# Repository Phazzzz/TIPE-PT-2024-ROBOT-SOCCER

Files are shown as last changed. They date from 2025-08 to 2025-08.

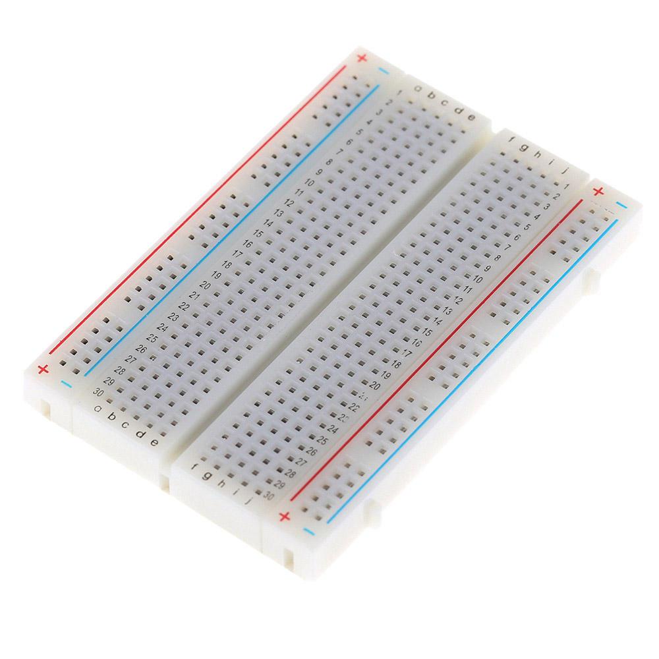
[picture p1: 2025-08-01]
Images illustrations/93206-desc-Quality-Solderless-Breadboard-400-Tie-Point-PCB-BreadBoard-for-Arduino-Interconnect-any-Components-with-20-29-AWG-(0.3-0.8)-wire-7-224400689.jpg

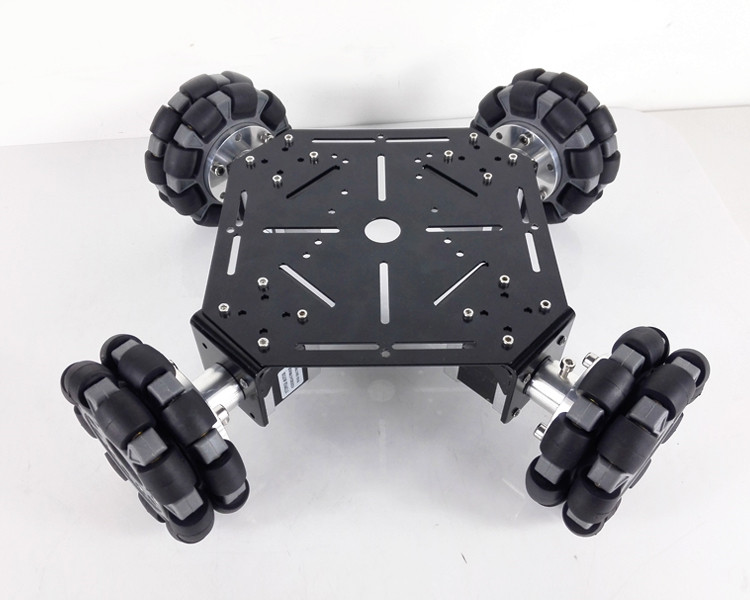
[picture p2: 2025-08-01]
Images illustrations/MT200S-4WD-100mm-Omni-Wheels-Robot-Car-Chassis-Stainsteel-Frame-Big-Power-Motor-For-DIY-Toy-2979076087.jpg

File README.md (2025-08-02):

# TIPE-PT-2024-ROBOT-SOCCER
Repo d'archive pour mon projet de TIPE que j'ai réalisé entre février 2023 et juin 2024 lorsque j'étais en prépa PT et pour lequel j'ai obtenu la note de 19,9/20. J'espère qu'il pourra aider de futurs taupins ! 

## L'histoire de ce TIPE

Comme tout taupin, je devais réaliser un projet de TIPE. C'était pour moi l'occasion de travailler sur un sujet qui plaisait réellement au milieu de tout les cours de prépas - qui ne sont pas tous passionnants, et dont l'utilité n'est pas toujours évidente. Ce projet a été mon exutoire en PTSI lorsque je n'avais pas envie de travailler mon prochain DS. 

Le thème de TIPE pour l'année 2023/2024 était "Jeux et sports", je savais dès le début que je voulais travailler sur un robot (même si je n'y connaissais strictement rien à l'époque) et ma première idée était de faire un robot de combat lol, mes profs me l'on déconseillé, car les sujets liés aux armes sont trop clivants auprès des correcteurs. La principale condition qu'ils m'avaient imposée était qu'il existe une ligue sportive pour le robot que j'allais réaliser. Je suis donc très rapidement tombé sur la Robocup, ce qui était la justification parfaite pour placer mon TIPE dans le thème de l'année. 

J'ai majoritairement travaillé sur ce projet durant l'année de PTSI (CF le DOT), j'ai d'abord commencé par faire le maximum de recherche sur comment fonctionne un robot pendant 1 mois et demi, puis j'ai acheté les composants pour faire un premier assemblage du robot, qui après à peu près 1 mois et de demie d'assemblage et de codage s'est avéré ne pas fonctionner. Durant l'année de PT, j'ai principalement fait de petites améliorations, changer quelques composants. J'ai surtout travaillé dessus entre les écrits et la date de rendu du projet (environ 3 semaines), j'ai passé 1 semaine à essayer de l'améliorer le plus possible, 1 semaine à faire toutes les expériences possibles pour justifier tout ce qui fonctionne et surtout tout ce qui ne fonctionne, puis 1 semaine pour faire le Powerpoint et travailler la présentation. 

D'après mon professeur de SI, la durée d'un bon TIPE est d'à peu près 50 à 70 h, personnellement, je suis plus proche des 350 h d'après mes estimations… Je n'ai évidemment aucun regret, mais je ne sais pas pour autant si je conseillerais d'en faire autant, car au final, mon projet était tellement ambitieux que la majorité du travail n'était pas présentable mais nécessaire à la réalisation du projet. Ce qui rajoute beaucoup de travail lors de la préparation de la présentation. D'ailleurs, je n'ai pas eu le temps de bien présenter la section "Présentation du robot" par manque de temps, je n'ai pu que la survoler, car je priorisais la conclusion.

## Pourquoi j'ai réussi cette épreuve selon moi 

#### J'ai kiffé réaliser ce projet
Comme dit plus haut, je me suis régalé pendant ce projet, j'ai tout réalisé moi-même, dessiner, imprimer des pièces en 3D, sélectionner les composant, faire l'assemblage, etc. Et j'ai bien appuyé sur ce point là pendant ma présentation. La pire chose qui puisse arriver pour un TIPE ambitieux est que le jury ne crois pas que vous l'ayez fais vous-même. La première question que le jury m'a posée était : "Où avez-vous acheté le robot ?", donc pendant toute la phase de réponse aux questions, j'ai donnée le maximum d'élément personnel pour justifier le fait que j'ai tout fais moi-même, sortir des photos, donner citer les références des composants (quand on a autant travaillé dessus ça finit par rentrer…), etc.

#### Faire un TIPE "original" et personnel
Un de mes profs en école me disait qu'il était correcteur l'année où j'ai passé mon TIPE, il a corrigé près de 70 TIPE portant sur la raquette de paddle… Donc, nécessairement, il devient difficile de ne pas s'endormir et tu deviens très exigeant dans la correction, la moyenne des notes qu'il donnait étaient autour de 9, et 14.5 étaient une bonne note selon lui.
Alors que lors de mon passage, avant de rentrer dans la salle, le correcteur m'avait très clairement fait savoir qu'il était curieux d'entendre mon travail. Alors qu'il y a beaucoup de TIPE qui sont plus technique, réalisé par des personnes plus talentueuses que moi, je pense que l'avantage de TIPE est que le sujet est plutôt cool. 

#### Être capable de tout justifier 
Ce que les correcteurs cherchent à voir, c'est que vous savez ce que vous faite, que cela fonctionne ou que cela ne fonctionne pas, ce n'est pas important tant que vous savez le justifier. Mon expérience était très clairement discutable (ce qu'ils n'ont pas manqué de faire), mais quand je leur explique que j'avais un problème sur un moteur, donc je ne pouvais faire qu'un mouvement de translation. J'ai dû faire les mesures de vitesse des roues par mesure vidéo (à vide ce qui est largement discutable) donc pour cela, j'ai fait une expérience qui démontrait clairement que les encodeurs étaient dysfonctionnels avec l'explication (trop d'interruptions dans le programme pour la prise de donnée).

#### Faire un beau Powerpoint
C'est plus accrocheur, ça permet de garder les correcteurs concentrés et ça permet de se démarquer.
Refaites vos schémas et équations directement dans Powerpoint ! Je sais que c'est long, ce n'est pas ultra passionnant, mais ça fait beaucoup plus sérieux, plus propre et c'est plus agréable à regarder. Les schémas dessinés à la main ne s'intègrent jamais très bien dans un Powerpoint.
Les Template de Powerpoint que j'ai utilisé sont dans le repo.

#### Bien penser sa présentation
J'ai commencé par les sections les plus importantes, à savoir la partie théorique et la partie expérimentale. J'ai mis la présentation du robot à la fin pour avoir la possibilité de sauter cette partie si je manquais de temps (ce qui a été le cas, il m'aurait fallu 1min30 de plus pour bien tout présenter). Réfléchir à toutes les questions que le jury pourrais poser et orienter leurs questions à l'aide de "Nous pourrons revenir sur ce sujet plus en détail plus tard". Ainsi, préparez-le plus d'annexe possible ! Il est toujours plus simple et rassurant de présenter à l'aide d'une diapo. Penser aussi à mettre les annexes que vous avez le plus de chance d'utiliser à la fin pour que les correcteurs voient toutes les annexes lorsque vous allez les faire défiler.

## Qu'est ce que l'on peut trouver dans ce repo ?
Ce repo contient absolument tous les documents que j'ai utilisé pour mon TIPE, ceux que j'ai récupéré sur Internet, et ceux que j'ai moi-même crée. LA présentation finale, le MCOT, le DOT, le code, mes notes (expérience, théorique, etc.), la documentation, les images, les diagrammes, etc. Je précise que tous les documents ne sont pas nécessairement libres de droits, vous pourrez trouver les références des images en notes de bas de pages dans le document "Présentation.pdf" et "Notes>Documentation externe".

## Remerciements
Merci à mon père et mes profs de prépa pour le soutien.
J'espère que ce repo pourra vous aider et bon courage pour les concours !

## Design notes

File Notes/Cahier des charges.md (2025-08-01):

| Fonction | Critère | Niveau |
| --- | --- | --- |
| Respecter les normes du concours | Masse | 1100g |
| | Encombrement | Diamètre max = 22cm |
| | Capacité de tir maximale | la balle ne doit pas excéder une distance sur une piste de 22cm incliné de 20° par rapport à l'horizontale |
| | Alimentation | Batterie 12V |
| | | |
| Déplacement | Se déplacer dans toute les directions | Déplacement holomnique |
| | Vitesse | Vitesse minimale = 2cm/s Vitesse souhaité = 1m/s (théorique) |
| | | |
| | | |
| | | |
| | | |

- Les robots doivent être construits et programmés pour se déplacer dans toutes les directions et toucher une balle placée à moins de 20 cm de n'importe quel point de leur coque convexe dans les 10 secondes.
- Kicker Power will be measured by means of an on-field test in Soccer Open and by means of the Kicker Power Measuring Device in Soccer Lightweight.
	- 1. Place robot inside the left corner of a goal. 2. Perform a kick into the opposing goal 3. The kicker power test is passed if after bouncing off of the opposite goal the ball does not return further than the front line of to the penalty area it was shot from.

- Le terrain de jeu mesure 158 cm sur 219 cm. Le terrain est marqué par une ligne blanche qui fait partie du terrain de jeu. Autour du terrain de jeu, au-delà de la ligne blanche, il y a une zone extérieure de 12 cm de largeur.

- it should be possible to kick them not just horizontally (as if in ”2D”) but also vertically (that is, to get the ball into the air).
- Les robots doivent être construits pour travailler dans des conditions qui ne sont pas parfaites

- Les robots doivent être construits et programmés de manière à ce que leur mouvement ne soit pas limité à une seule dimension.

- Tous les robots doivent avoir une poignée stable et facilement visible pour les tenir et les soulever. La poignée doit être facilement accessible et permettre au robot d'être ramassé à au moins 5 cm au-dessus de la structure la plus élevée du robot.

- A robot may use any number of cameras without restrictions on lenses, optical parts, optical sys- tems,andtotalfieldofview.Componentsmaybesourcedinanywaytheteamseesfit.

- 1. Démarrage du robot dans la zone de pénalité, orienté vers le but
    - Point de départ : Zone de pénalité
    - Orientation : Vers le but
- Les balles utilisées dans le jeu ont des spécifications précises concernant leur diamètre, leur résistance, leur couleur et leur fonctionnement.

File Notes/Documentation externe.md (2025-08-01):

#### Ressource général 

[3D find it , le trouve tout de la 3D](https://www.3dfindit.com/fr/)

[Référence language Arduino](https://www.arduino.cc/reference/en/)

[Github Arduino](https://github.com/arduino/docs-content)https://fr.overleaf.com/learn/latex/List_of_Greek_letters_and_math_symbols

[Référence Latex](https://fr.overleaf.com/learn/latex/List_of_Greek_letters_and_math_symbols)
#### Cours 

##### [Excellent Tuto asservissemennt vitesse](http://www.ferdinandpiette.com/blog/2012/04/asservissement-en-vitesse-dun-moteur-avec-arduino/)

[Cours complet conception robot holonome](https://www.studica.co/resources-4)

[Explication déplacement Holomnique Facile](https://www.servomagazine.com/magazine/article/a-look-at-holonomic-locomotion)

[Fonctionnement Encodeur](https://www.generationrobots.com/blog/fr/encodeurs-robotique-mobile/#:~:text=Un encodeur est un dispositif,chacune des roues du robot.) 

[Dynamics of a four-wheeled mobile robot with Mecanum wheels](https://onlinelibrary.wiley.com/doi/full/10.1002/zamm.201900173)

#### Exemple autre projet

[Projet Robot Soccer](https://robot-soccer-kit.github.io/hardware-robots#motors-and-wheels)
[Modèle 3D Robot Soccer](https://cad.onshape.com/documents/c5fe05581d14c59bfb08f79e/w/a8cb82e3a358c0b06e1cbf91/e/f45372d8263c18466905bd9b)

##### Site commerce : 

- [RobotShop](https://www.servomagazine.com/magazine/article/a-look-at-holonomic-locomotion)

#### Design electronique

Protheus Visual Designer for Arduino

[https://www.multipower.fr/boutique/visual-designer/](https://www.multipower.fr/boutique/visual-designer/)

https://www.multipower.fr/software/cao_proteus/proteus-visual-designer/

[https://www.theengineeringprojects.com/2021/03/arduino-mega-2560-library-for-proteus-v2-0.html](https://www.theengineeringprojects.com/2021/03/arduino-mega-2560-library-for-proteus-v2-0.html)

### [TUTO SIGMA ASSERVISSEMENT POSTION/VITESSE](https://blog.3sigma.fr/arduino/tutoriel-arduino-asservissement-en-vitesse-dun-moteur-a-courant-continu/)
#### Librairie Arduino digitalWrite fast :

- "Vous aurez peut-être remarqué l’utilisation de la fonction **digitalReadFast2()** pour lire le niveau des entrées codeur, au lieu de la fonction standard **digitalRead()**. Cette fonction, issues de la librairie **digitalWriteFast** (téléchargeable à l’adresse [http://www.3sigma.fr/telechargements/digitalWriteFast.zip](http://www.3sigma.fr/telechargements/digitalWriteFast.zip)) permet d’améliorer la rapidité de lecture et d’écriture des entrées digitales pour minimiser le temps passé dans la routine d’interruption (et donc rendre la main plus vite à la boucle de calcul principal). Pour utiliser cette bibliothèque dans votre code, vous devez faire deux choses simples"

For a 16 MHz Uno digitalWrite() is speed up from 5.8 µs to 125 ns, able to generate a 4 MHz signal instead of 86 kHz. [SOURCE CHIFFRE](https://github.com/ArminJo/digitalWriteFast)
#### Utilisation de delay() :

Pour que cela fonctionne correctement, ce code doit être exécuté à la cadence fixe de 0.01 s. L’utilisation de la fonction **delay()** pour faire ça est une **mauvaise** méthode. En effet, vous pourriez penser écrire le code suivant :

| | |
| --- | --- |
| 1<br><br>2<br><br>3<br><br>4<br><br>5<br><br>6<br> | `void` `loop() {`<br><br>  `// Traitements divers`<br><br>  `// Lecture d'entrées + calculs par exemple`<br><br>  `// Attente de 10 ms`<br><br>  `delay(10);`<br><br>`}` |

Le problème est que les « traitements divers » vont prendre un certain temps, inconnu (T) et potentiellement variable (dans le cas où ils incluent des instructions conditionnelles). Par conséquent, la boucle sera exécutée toutes les T+0.01 s et non pas toutes les 0.01 s, et la mesure de la vitesse de rotation sera fausse.

La bonne méthode consiste à utiliser un timer du microcontrôleur pour générer une interruption toutes les 0.01 s. Vous pouvez utiliser pour cela la bibliothèque FlexiTimer2 (téléchargeable ici: [http://www.3sigma.fr/telechargements/FlexiTimer2.zip](http://www.3sigma.fr/telechargements/FlexiTimer2.zip)). Après l’avoir décompressée, il faut la placer dans le sous-répertoire « librairies » de l’installation de l’environnement de développement Arduino et ajouter au début du programme la ligne :

Enfin, il faut ajouter les deux lignes suivantes dans la fonction **startup()** :

| | |
|---|---|
|1<br><br>2|`FlexiTimer2::set(10, 1/1000., isrt);` `// résolution timer = 1 ms`<br><br>`FlexiTimer2::start();`|

La première ligne crée une interruption qui se produit toutes les 10 ms (avec une résolution de 1 ms), ce qui exécute alors la fonction **isrt()** (contenant le code permettant de calculer la vitesse de rotation et de réaliser l’asservissement de vitesse). La seconde ligne démarre ce timer.

------

[attachInterrupt function reference](https://www.arduino.cc/reference/en/language/functions/external-interrupts/attachinterrupt/)
### Interrupt Numbers

Normally you should use `digitalPinToInterrupt(pin)`, rather than place an interrupt number directly into your sketch. The specific pins with interrupts and their mapping to interrupt number varies for each type of board. Direct use of interrupt numbers may seem simple, but it can cause compatibility trouble when your sketch runs on a different board.

However, older sketches often have direct interrupt numbers. Often number 0 (for digital pin 2) or number 1 (for digital pin 3) were used. The table below shows the available interrupt pins on various boards.

Note that in the table below, the interrupt numbers refer to the number to be passed to `attachInterrupt()`. For historical reasons, this numbering does not always correspond directly to the interrupt numbering on the ATmega chip (e.g. int.0 corresponds to INT4 on the ATmega2560 chip).

| BOARD | INT.0 | INT.1 | INT.2 | INT.3 | INT.4 | INT.5 |
| --- | ----- | ----- | ----- | ----- | ----- | ----- |
| Mega2560 | 2 | 3 | 21 | 20 | 19 | 18 |
| | | | | | | |

For Uno WiFi Rev2, Due, Zero, MKR Family and 101 boards the **interrupt number = pin number**.

----------------

## Fonction map()

Re-maps a number from one range to another. That is, a value of **fromLow** would get mapped to **toLow**, a value of **fromHigh** to **toHigh**, values in-between to values in-between, etc.

Does not constrain values to within the range, because out-of-range values are sometimes intended and useful. The `constrain()` function may be used either before or after this function, if limits to the ranges are desired.

**Note that the "lower bounds" of either range may be larger or smaller than the "upper bounds" so the `map()` function may be used to reverse a range of numbers, for example**

### `y = map(x, 1, 50, 50, 1);`

-------

### Broches analogiques Arduino Mega 2560 Rev3

Mega 2560 dispose de 16 entrées analogiques, chacune pouvant fournir une mesure d’une résolution de 10 bits (càd sur 1024 niveaux soit de 0 à 1023) à l’aide de la très utile fonction analogRead() du langage Arduino. Par défaut, ces broches mesurent entre le 0V (valeur 0) et le 5V (valeur 1023), mais il est possible de modifier la référence supérieure de la plage de mesure en utilisant la broche AREF et l’instruction analogReference() du langage Arduino.

---------------------------

https://www.comptoir-du-cable.com/content/7-calcul-section-cable-electrique#tableau_cinq

![[Longueur maxi en câble cuivre alimentation monophasé 230V.png]]

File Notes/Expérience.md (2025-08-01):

#### Expérience 1 : Précision de déplacement du robot

Réaliser plusieurs motif cyclique de différentes complexité, ainsi en mesurant l'écart entre le point de départ et d'arrivé on peut définir une précision 

- Un carré, avance, tourne, avance, etc.
- un triangle équilatérale, selon les axes des moteurs 
- un cercle 
- le robot translate en décrivant un cercle tout en tournant sur lui même.

-----

#### Expérience 1 : V2 de secours : Précision déplacement selon l'axe de 1 moteur 

- Calcul de consigne à partir de la partir théorique 
- Donner ces vitesses en consigne durant un temps définie 
- Mesurer la distance parcourut par le robot 
- Comparaison avec la distance théorique parcourut par le robot 

###### Bonus : Vérifier la vitesse obtenue par les encodeurs à fin de validé leurs fonctionnement

Hypothèse : 
- Le robot va parfaitement droit 
- On néglige la baisse de tension de la batterie

###### Résultats expérience :

| | bit | bit | | | | |
| --- | --- | --- | --- | ----- | --- | --- |
| N° | Moteur 1 | Moteur 2 | Distance | Temps | Statut | |
| 1 | 240 | 100 | 130cm | 5s | Invalide | |
| 2 | 240 | 110 | 145cm | 4.8s  | Invalide | |
| 3 | 250 | 110 | 148cm | 5s | Valide | |
| 4 | 250 | 110 | 148cm | 5s | Valide | |
| 5 (chambre) | 250 | 110 | 110cm | 3s | Valide | |

Mesure encodeur moteur 1 : 11.55 rad/s
Revêtement : parquet synthétique 

###### Calcul exp.  :
V : Vitesse du robot 

Pour les expérience 3 et 4 :
$$
V = \frac{148}{5} * 10 = 296 mm/s
$$
Pour l'expérience 5 :
$$
V = \frac{110}{5} * 10 = 367 mm/s
$$
D'après l'étude cinématique :

- Pour les expérience 3 et 4 :
 $$
\begin{split} 
\omega = \frac{\sqrt{3}}{29\times2}\times V  \\ \\
A.N : \omega =   \frac{\sqrt{3}}{29\times2}\times 296 = 8.84 rad/s
\end{split}
$$
- Pour l'expérience 5 :
$$
\begin{split} 
A.N : \omega =   \frac{\sqrt{3}}{29\times2}\times 366 = 11 rad/s
\end{split}
$$

##### Validation Vidéo :

- Moteur 1 :
	- Début : 5,41s
	- Fin : 5,84s 
	- Durée : 0,43s
	- $\omega1 = \frac{2\pi}{0.43} = 14,61$ rad/secondes

	- Début : 7,07s
	- Fin : 7,50s 
	- Durée : 0,43s
	- $\omega1 = \frac{2\pi}{0.43} = 14,61$ rad/secondes

- Moteur 3 :
	- Début : 7,19s
	- Fin : 7,62s 
	- Durée : 0,43s
	- $\omega1 = \frac{2\pi}{0.43} = 14,61$ rad/secondes 

----------------------------------------------------

#### Expérience 2 : Mesure : évolution de la vitesse maximale / consigne

Tracé : 
- Ordonnée : Vitesse maximale 
- Abscysse : consigne en % (consigne/255*100)
- Pas de la consigne : 25 bits

Comparer 2 test : 
- Test 1 : avec 1 moteur sollicité
- Test 2 : avec 2 moteurs sollicités

----

#### Expérience 3 : Encodeurs

- ###### 1 Moteur en fonctionnement :
	- Mesure : 
		- Début : 2.31
		- Fin : 2.58
	- $\rightarrow \omega = \frac{2\pi}{0.27} = 23.27$ rad / seconde

- Valeur mesuré par l'encodeur : 23 rad/s
- Conclusion : Validé

- ###### 2 Moteur en fonctionnement :
	- Mesure : 
		- Début : 3.26
		- Fin : 3.55
	- $\rightarrow \omega = \frac{2\pi}{0.29} = 21.66$ rad / seconde

	- Valeur mesuré par l'encodeur : 11.55 rad/s
	- Conclusion : Incohérent 
		- Hypothèse : Trop d'interruption donc le comptage des ticks est faussé

---

#### Mots clés

[[Documentation externe]]
[[Fiches Techniques]]
[[Note de code]]
[[Note de suivie]]
[[Fiches Techniques]]

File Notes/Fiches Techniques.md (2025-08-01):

#### [Arduino : Mega 2560 Rev3](https://arduino-france.site/description-arduino-mega/)

[https://docs.arduino.cc/hardware/mega-2560](https://docs.arduino.cc/hardware/mega-2560)

datasheet [https://docs.arduino.cc/static/4a7c7ca5a5e6a633d7f6ccbd3aee8560/A000067-datasheet.pdf](https://docs.arduino.cc/static/4a7c7ca5a5e6a633d7f6ccbd3aee8560/A000067-datasheet.pdf)

PWM : [https://passionelectronique.fr/pwm-arduino/](https://passionelectronique.fr/pwm-arduino/)

| | |
| --- | --- |
| Broche d'interruption | Pin |
| 0 | 2 |
| 1 | 3 |
| 2 | 21  |
| 3 | 20  |
| 4 | 19  |
| 5 | 18  |
| | |

#### Motoréducteurs :

- Alimentation: 6 Vcc (7,5 Vcc maxi)
- **Vitesse à vide: 295 tours/min**
- **Rapport de réduction: 34:1**
- Consommation à vide: 0,35 A
- Consommation moteur bloqué: 5,5 A
- Couple moteur bloqué: 4,0 kg.cm
- Axe: Ø4 x 10 mm avec méplat
- Dimensions: Ø25 x 77 mm (axes inclus)

https://www.gotronic.fr/art-motoreducteur-wt341-17752.htm

Motoréducteur économique pour applications en robotique.

#### Encodeurs :

- **Résolution : 544 tick par tour 

![[Encodeur RS003 Fiche technique.pdf]]

[https://www.gotronic.fr/art-motoreducteur-34-1-encodeur-rs003-24295.htm](https://www.gotronic.fr/art-motoreducteur-34-1-encodeur-rs003-24295.htm)

[https://www.gotronic.fr/pj2-34164-rs003-enco-1611.pdf](https://www.gotronic.fr/pj2-34164-rs003-enco-1611.pdf)

https://www.robot-maker.com/shop/blog/32_Utilisation-des-encodeurs.html

#### Roues :

- Diamètre = 58mm 
- Moyeu : 4mm
- Largeur : 26.5 mm 
- Poids : 89g par roues
- Longueur des rouleaux : 18 mm
- Poids maximal supporté 12 Kg
- Matériaux : plastique ABS et aluminium sablé 
- Nombre de rouleaux : 5
- Matière des jantes : Aluminium
- Couleur des jantes : Acier
- Couleur des rouleaux : Noir

ZK 5AD

1.     Product Name: 5A Dual Motor Drive Module
2.     Product Number: ZK-5AD
3.     Working Voltage: DC 3.0V-14V
4.     Input Signal Voltage:DC 2.2V-6.0V
5.     Drive Current: 5A
6.     Stand-by Current:10uA
7.     Working Temperature range: -20℃~85℃
8.     Working Humidity range: 0%-95%RH
9.     Size:38*27*18mm
10.     Mounting hole diameter:2mm

**Réducteur de tension / Régulateur de Tension**

Attention au drop out voltage ( 2V sur un LM7805 !!) https://riton-duino.blogspot.com/2018/11/les-regulateurs-ldo.html

[https://www.amazon.fr/dp/B08Q8K5342/](https://www.amazon.fr/dp/B08Q8K5342/)

[https://www.amazon.fr/DollaTek-r%C3%A9gulateur-bornes-lentr%C3%A9e-LM7805/dp/B081JMJZG6](https://www.amazon.fr/DollaTek-r%C3%A9gulateur-bornes-lentr%C3%A9e-LM7805/dp/B081JMJZG6)

[https://sonelec-musique.com/electronique_theorie_reg_tension.html](https://sonelec-musique.com/electronique_theorie_reg_tension.html)

**Driver L9110**

[https://www.robot-maker.com/shop/drivers-d-actionneurs/56-driver-moteurs-cc-l9110-56.html](https://www.robot-maker.com/shop/drivers-d-actionneurs/56-driver-moteurs-cc-l9110-56.html)

[https://www.robot-maker.com/forum/topic/11228-driver-l9110-pour-moteur-cc-teste-par-mthibs/](https://www.robot-maker.com/forum/topic/11228-driver-l9110-pour-moteur-cc-teste-par-mthibs/)

Max current 2A

#### Capteur à ultrasons :

- Ref : HC-SR04
-

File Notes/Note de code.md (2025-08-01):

| Pin | Fonction | Couleur fil | Nom Pin | |
| --- | --- | :--- | --- | --- |
| | | | | |
| Broche Interruption | | | | |
| 2 | Encodeur 1A | Blanc<br> | interrupt 0 | |
| 3 | Encodeur 1B | Jaune | interrupt 1 | |
| | les pins de enco 1 ont temporairement été branché sur les pins de enco 2 et enco 2 n'est plus branché | | | |
| 18 | Encodeur 2A | Blanc | interrupt 5 | |
| 19 | Encodeur 2B | Jaune | interrupt 4 | |
| | | | | |
| 20 | Encodeur 3A | Blanc | interrupt 3 | |
| 21 | Encodeur 3B | Jaune | interrupt 2 | |
| | | | | |
| | | | | |
| PWM | | | | |
| 8 | Vitesse moteur 1 | Vert | D3 (Solo) | |
| 10 | Vitesse moteur 2 | Blanc | D3 (Duo) | |
| 12 | Vitesse moteur 3 | Jaune | D1 (Duo) | |
| | | | | |
| Digital | | | | |
| 50 | Sens moteur 1 | Jaune | D2 (Solo) | |
| 51 | Sens moteur 2 | Vert | D2 (Duo) | |
| 52 | Sens moteur 3 | Orange | D0 (Duo) | |

## Formules 

- vitesse au sol : v = $\omega \times 2 \pi \times Rayon$

## Valeurs expérimentales
#### Masses : 

Chassis bas + chassis haut = 248g
Supports moteurs : 3 x 50g = 150g
entretoises : 6 x 12g = 72g

#### Expérience moteur :

| | | | | |
| --- | --- | --- | --- | --- |
| | | | | |
| Moteur : | Temps Caractéristique | Mesure | Vitesse au sol | K |
| Moteur 1 | T1 = | | | |
| Moteur 2 | T2 = | | | |
| Moteur 3 | T3 = 0.055s | 164ms pour aller à 191 tr/min, consigne : 255 bits ($\leftrightarrow$ 5V) | $v3 = \frac{191 \times 2 \pi \times 29}{60} = 580 mm/s$ | $K = \frac{580}{255} = 2.27 mm/tick$ |
| | | | | |
| Résistance interne | | | | |
| Moteur de secours  | R = 1.8 ohm | | | |

##### Cas :
- 2 moteurs à la même vitesse dans le même sens : RAS
- 2 moteurs à deux vitesses 
### Expérience Drivers
#### Table logique driver moteur et bit de seuil 

| MOTEUR 1 | Sens | PWM |
| --- | --- | --- |
| Rotation Horaire vitesse maximale | LOW | 255 |
| Rotation Horaire vitesse minimale | LOW | 38 |
| | | |
| Rotation anti-Horaire vitesse maximale | HIGH | 0 |
| Rotation anti-Horaire vitesse ***minimale*** | HIGH | 245 |
| | | |
| | **Sens** | **PWM** |
| MOTEUR 2 | LOW | |
| Rotation Horaire vitesse maximale | LOW | |
| Rotation Horaire vitesse minimale | | |
| | HIGH | |
| Rotation anti-Horaire vitesse maximale | HIGH | |
| Rotation anti-Horaire vitesse ***minimale*** | | |
| | | |
| MOTEUR 3 | **Sens** | **PWM** |
| Rotation Horaire vitesse maximale | LOW | 255 |
| Rotation Horaire vitesse minimale | LOW | 60 |
| | | |
| Rotation anti-Horaire vitesse maximale | HIGH | 0 |
| Rotation anti-Horaire vitesse ***minimale*** | HIGH | 236 |

----------------------

### Valeurs calculés :

- (Fiche technique ) Vmax moteur = 295 tr/min
- Vitesse max du moteur à 5V : Vmax théorique = $\frac{5}{6} \times \frac{295 \times 2 \pi \times 29}{60} = 746 mm/s$
- Rendement : r = $\frac{V,max,mot,3}{Vmax,théorique} = \frac{580}{746} = 0.77$ (Nota bene : calcul réalisé avec la vitesse max expérimentale du moteur 3)

#### Encodeurs :

- Chgmt d'états : 544 tick/tr (fiche technique)

- Résolution = $\frac{2\pi}{544} = 0.01$  rad/tick
- Précision = $Périmètre*Résolution = 29*0.01 = 0.029 \approx 0.03$ **mm/tick 

- ***Vitesse au angulaire*** : $v = \frac{d}{t} = \frac{2\pi\times ticks \times 1000}{dt}$ rad/seconde
- ***Vitesse au sol*** : $v = \frac{d}{t} = \frac{2\pi\times ticks \times 1000}{dt}$ rad/seconde

-----

### Equations :

	Angle : a = arctan(dy/dx)

	A : dx

	BD : dx*cos(a) + dy*sin(a)

	BG : dx*cos(2*a) + dy*sin(2*a)

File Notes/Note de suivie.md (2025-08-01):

Enco 1 a été branché sur les ^pins de enco 2 
Enco 2 est débranché 

Problème avec les interruptions sur les pins 2 et 3 (enco 1 fonctionne)
en revanche durant le test les moteurs ne démarraient plus 

Problème régler en révisant la [[Note de code#Table logique driver moteur|Table logique driver moteur]] En revanche le moteur 2 semble mort (gros frottement interne)

Problème avec la vitesse de rotation calculée par le programme (voir feuille de calcul) 

En mesurant avec les codeurs incrémentaux (je précise que les valeurs sont peut-être fausses mais ca montre la différence entre les vitesse avec des moteurs lorsque 1 seul est sollicité, et lorsque 2 moteurs sont sollicité) j'ai 23rad/s pour 1 moteur, et 11,55 rad/s lorsque 2 moteurs sont sollicités

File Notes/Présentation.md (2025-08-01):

Expérience : Précision de déplacement du robot 

### Déroulé : **Temps totale : (15min)**

-          Présentation du contexte **(1min)**

-          Description du robot (Diagramme de définitions, schéma électrique, etc) **(3min)**

-          Cinématique du robot omnidirectionnel **(4min)**

-          Présentation du code informatique **(3min)**

-          Compte rendu de l’expérience **(3min)**

-          Conclusion **(1min)**

##### Bonus :

-          Conception des supports moteurs

-          Calcul d’asservissement ? (PID)

### Présentation du contexte 

- Présentation (rapide) Robocup 
- Diagramme des cas d'utilisations
	- Se déplacer sur le terrain
		- Ne pas sortir des limites du terrain
		- Déplacer la balle
	- Intercepter la balle 
	- Tromper l'adversaire
	- Tirer la balle 
	- Faire une passe à son coéquipier
- - Problématique 
	- Comment tirer un pénalty capable de tromper le gardien avec un robot soccer ?
-  Identification des besoins
	- Agilité 
	- rapidité
- Cahier des charges

### Présentation du robot 

- Choix de constructions
	- Déplacement Holomnique 
	- Robot à trois roues 
- Architecture générale 
	- Diagramme d'exigence
	- Diagramme de bloc interne

### Cinématique du robot omnidirectionnel

- Les objectifs de l'études
- Paramétrage 
- Etude de la translation sur x0

### Expérience 

- Déplacement du robot selon l'axe d'un moteur  
- Consigne à envoyer au moteur issue de la partie théorique 
- Expérience 1 : mesure de vitesse robot
	- Protocole
		- Faire avancer le robot sur 148cm (limite de la longueur du cable entre l'Arduino et l'ordi) et mesurer le temps que met le robot à parcourir la distance 
	- Hypothèses et incertitude
	- Résultat
- Expérience 2 : mesure rotation des roues 
	- Protocole
	- Résultat

### Présentation du code informatique 
##### Qu'est ce qu'il fait  ?
-    Initialisation 
	- Définition des constantes 
- Pilotage des moteurs 
- Encodeurs 

### Résultat d'expérience 

### Les petites expériences 

- Note de code#Table logique driver moteur|Table de consigne des drivers moteurs
- Note de code#Valeurs expérimentales#Valeurs calculés|Constantes fonction de transfère moteurs
- Note de code#Encodeurs|Constantes fonction de transfère encodeurs
- Note de code#Valeurs calculés|Comparaison vitesse max théorique et vitesse max mesurée
	- Vérification du cahier des charges 

### Les problèmes 

- Sous dimensionnement de la chaine de puissance :
	- Cables électriques
		- voir Diagramme
	- Driver
		- Comparaison du courant entre l'ancien et le nouveau :
	- Abaisseur de tension
		- Courant
	- Batterie 
		- Calcul de puissance :
			- Consommation moteur : $P = tension \times courant = 6 \times 15 = 90Watt$
			- Batterie : 24,4Wh -> $24,4\times3600 = 87840 Watt/s$

- Moteur qui ne fonctionne pas 
	- Difficile à tourner 
		- Couple statique très élevé sans raison 
- 

Consigne
T_(1 tour)
ω

### Temps additionnel 

- Détail des calcul de la partie théorique 

- Problèmes rencontrés 
	- Transmission électrique 
	- moteur

- Explication Omniwheels
	- Avantage 
		- Manoeuvrabilité 
	- Inconvénient 
		- Manque d'adhérence 
		- Vibration 
			- Améliorer en mettant plus de petit rouleaux et plus de ranger  
		- Besoin d'un couple plus important qu'un système classique
			- Exemple : tourner une poigné mais en y mettant de l'angle 
	- Omni à 3 roues
		- + Stable (3 points = 1 plan)
		- + simple à réaliser (mais un peu plus dure à coder)
	- Omni à 4 roues :
		- Mécanisme plus complexe (mais un peu plus simple à coder)
			- 4 moteurs à gérer
			- Problème de planéité 
			- Encombrement
		- Amélioration de l'adherence 
		- Amélioration du couple 
			- + de moteur = + de puissance
			- Permet d'utiliser plus de moteur pour un même mouvement 

- Modélisation des supports de drivers et les supports moteurs
## Attendus pédagogique

##### Objectif principaux :

- maintenir un questionnement scientifique sur toute la durée de son projet 

-  mettre en relief les choix qu’il aura dû faire au cours de son étude, la cohérence, ainsi que la densité du travail réalisé

- à clairement faire apparaître l’originalité de sa contribution par rapport à celles des autres membres de son groupe dans le cas d’un projet à plusieurs membres.

## Attendus de présentation

- **Il est fortement recommandé aux candidats de placer leur numéro d'inscription en première page, et de numéroter toutes les diapositives, afin de faciliter l’entretien avec les examinateurs.**

- format PDF2 
- ne doit pas dépasser 5 Mo.
- Il ne pourra pas contenir de vidéos, de fichiers audio, ni d'animations notamment du type Powerpoint
- Il n'y a pas de nombre limité de pages ni de mots
	- (Conseil) : au grand maximum 10 lignes par diapositive
- adjoindre autant que possible une iconographie adaptée (graphiques, schémas, photographies, images) venant en complément du texte et de l'exposé associé.
	- Toute illustration extraite d’une source externe devra être référencée, par exemple en bas de diapositive, en bonne et due forme afin qu’il n’y ait pas d’ambiguïté sur son origine.

Spécifique à chaque membre d'un éventuel groupe, le support de présentation doit être propre à chaque candidat et correspondre à son objectif individuel. Seul un petit nombre de diapositives peuvent introduire ou reprendre le projet du groupe.

Cette présentation doit être téléversée sur le site SCEI rubrique SCEI>Mon_Dossier>TIPE. L'absence de dépôt pourra conduire à l’attribution de la note zéro à l’épreuve. Dans tous les cas, le candidat devra vérifier la présentation téléversée afin de s’assurer qu’elle pourra être ouverte et utilisée lors de son passage en salle d’oral. Pour ce faire, il est conseillé de l’afficher à partir du serveur SCEI.

###### Programme informatique : 
Si le candidat a développé des programmes informatiques, il devra apporter en double exemplaire les listings correspondants sur support papier. Ces listings seront également inclus en documents annexes à la présentation (en aval de la conclusion) mais ne seront pas présentés formellement durant l’exposé du candidat. Ils pourront faire l'objet de questions spécifiques lors de la phase d’échange avec les examinateurs. Il est fortement recommandé d’afficher ces listings sur fond blanc pour être plus lisibles

##### Critères d'évaluation 

- Potentiel Scientifique :
	- Pertinence et justesse scientifiques
	- Appropriation et capacité à apprendre
	- Ouverture & Curiosité
- Démarche Scientifique :
	- Questionnement et Méthode 
	- Résolution de problème 
	- Communication - Présentation - Échange

##### Référence illustration

Match robocup junior : https://www.iceberg-robots.de/2019/08/27/robocup-german-open-2019/

Match robocup : https://www.robocup.org/leagues/19

robocup match humanoide : https://www.indramat-us.com/robocup/

robocup-junior1-1247468535 : https://de.mathworks.com/academia/student-competitions/robocup-junior.html

maxresdefault-935886106.jpg : https://www.youtube.com/watch?v=gZ-AAXpM4U4

Logo Robocup : https://robocuprussiaopen.ru/en/events/russiaopen/2019/

Schema déplacement robot omni : https://www.servomagazine.com/magazine/article/get-rolling-with-omni-directional-wheels

Comparaison des roues omni : https://www.omnitrack.com/product-category/wheels-castors/omniwheels/

Robot omni 4 roue : https://www.aliexpress.com/item/MT200S-4WD-100mm-Omni-Wheels-Robot-Car-Chassis-Stainsteel-Frame-Big-Power-Motor-For-DIY-Toy/32841507269.html

Roue mecanum : https://www.artstation.com/marketplace/p/rPw2/3d-mecanum-wheel

L7806 : https://thaipick.com/product/lazada/2221014

Jumper Wire : https://udvabony.com/product/male-to-female-jumper-wire-single/

Breadboard : https://cukii.com/product/quality-solderless-breadboard-400-tie-point-pcb-breadboard-for-arduino-interconnect-any-components-with-20-29-awg-(0.3-0.8)-wire

Moteur : https://www.gotronic.fr/art-motoreducteur-34-1-encodeur-rs003-24295.htm

Batterie : https://rcsearch.info/-c11374

Abaisseur de tension : https://www.alibaba.com/product-detail/Factory-Tobsun-12v-24v-To-5v_1600627269932.html

Fil Tuofeng : https://www.carousell.sg/p/tuofeng-22-gauge-pvc-electrical-wire-30-meter-reel-2-pin-extension-cable-12v-24v-dc-cable-wire-for-single-led-strip-light-1098966592/

L9910 :https://gethacking.com/products/dc-stepper-motor-driver-board

ZK-5AD : http://aquaphoton.net/product/zk-5ad-5a-dual-dc-motor-drive-module/

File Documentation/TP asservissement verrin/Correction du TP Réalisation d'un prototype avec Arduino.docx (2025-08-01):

Correction du TP vérin électrique asservi avec Arduino

Question :

La tension de saturation du moteur est 12 V.

Le seuil se produit pour la valeur Vit=35, soit une tension Us=12*35/255=1.65V (en supposant que la tension maxi est 12V).

Question :

X= 0mm ÞPot_V=20

X=205 mm ÞPot_V=993

X=map(Pot_V,20,993,0,205) ;

X=map(Pot_V,20,993,0,2050)/10 ;

Question : L’erreur de quantification est e=205/(993-20)=0.21 mm

Dir=((Xref-X)>0);

(Xref-X)>0 renvoie 1 si vrai, 0 si faux. Cela évite de faire le test suivant :

if (Xref>X) {Dir=1 ;} else {Dir=0 ;}

Question : On identifie le moteur à un système d’ordre 1.

On atteint 95% de la consigne après 0.3s, donc T=0.1s

255 points donnent une vitesse finale de 24 mm/s donc K=24/255=0.094 mm/s.pts

Question :

- La saturation se produit quand Vit=255, donc quand, soit :
- Le seuil se produit quand Vit=35, donc quand, soit :

Théoriquement, l’écart statique devrait être de 3.5 mm, mais on trouve expérimentalement un écart statique de 0,8mm. Cet écart est dû au seuil, qui peut donc être plus petit si le moteur est déjà en marche.

On peut réduire cet écart en augmentant Kp. Pour Kp=40, on trouve un écart statique de 0,2 mm.

Question : IA=I*5/(1023*1.65);

Question :

if (IA<IMax) {temps=millis();} // Relevé du début de la surcharge

if ((millis()-temps)>500) {arretMot=1;} // La surcharge dure plus de 500 ms

Question : Le correcteur proportionnel produisait un écart statique du au seuil du moteur.

Une intégration dans le correcteur annulera l’écart statique, même en présence de perturbations et le système sera conforme au cahier des charges.

Question : Avec le correcteur , , et la phase est toujours inférieure à 180°.

Il n’y a donc aucune possibilité de stabilité.

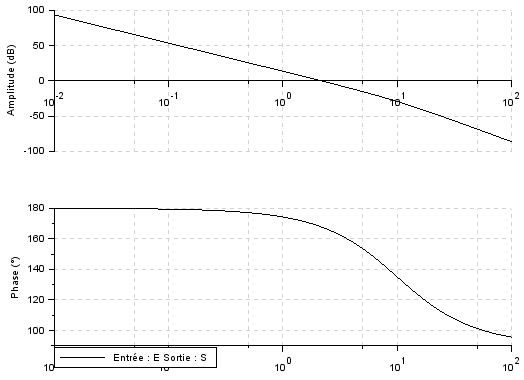
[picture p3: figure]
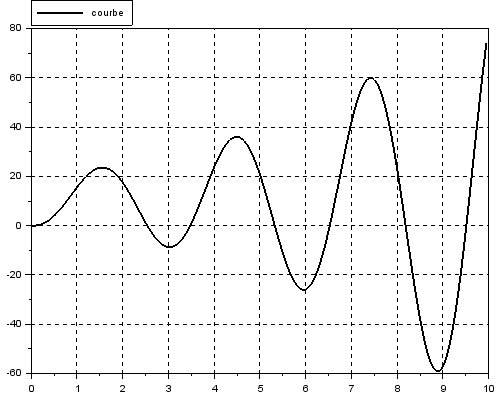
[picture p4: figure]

Phase inférieure à -180° modulo 360° Réponse impulsionnelle divergente

Question : Si a<1, la phase est toujours inférieure à -180°, donc il n’y a pas de possibilité de stabilité.

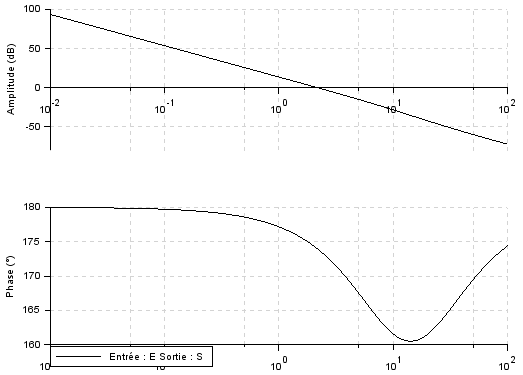
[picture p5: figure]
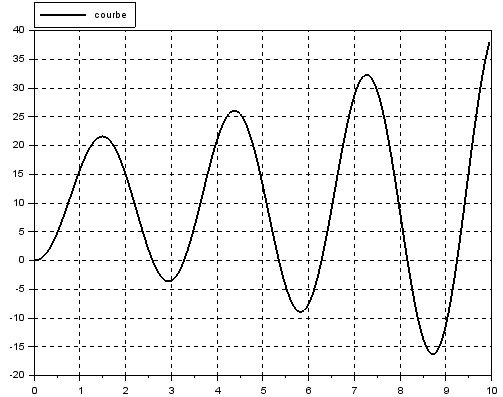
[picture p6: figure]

Phase inférieure à -180° modulo 360° Réponse impulsionnelle divergente

Question : a=7.55 donne une remontée de phase jusque -130°

Question : Ki=49 donne une marge de phase Mφ=50° conforme au cahier des charges. Kp=7.55*0.1*Ki=37

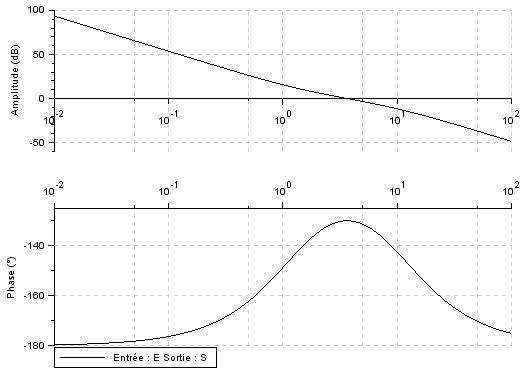
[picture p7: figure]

Question : On ajoute la sturation

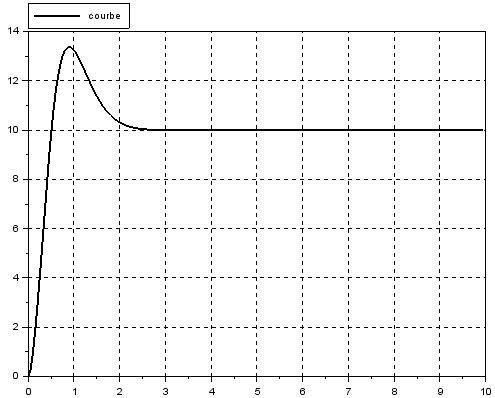
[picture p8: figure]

- Ecart statique nul, même en présence de perturbations car il y a une intégration avant la perturbation.
- Marge de phase Mφ=50°
- Temps de réponse à 5 % inférieur à 3s pour un échelon de 10 mm
- Premier dépassement inférieur à 4 mm

Pourtant, le modèle n’est pas conforme au cahier des charges car pour un échelon de 100 mm, la saturation fait augmenter énormément le premier dépassement qui dépasse 80 mm.

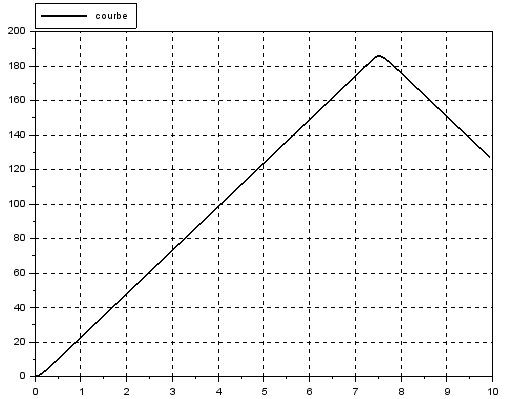
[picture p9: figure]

Ki=49 et Kp=7.55*0.1*Ki=37

Question :

D1=3.4 mm pour un échelon de 10 mm

D1 = 86 mm pour un échelon de 100 mm

Performances attendues | Performances mesurées | Performances simulées
Ecart statique nul, même en présence de perturbations (tolérance ±0.2 mm) | Conforme εS=0.2 mm Conforme | Ecart du à la résolution du capteur εS=0 mm
Marge de phase Mφ=50° | Conforme Pas vérifié mais stable | Mφ=50°
Temps de réponse à 5 % inférieur à 3s pour un échelon de 10 mm | Conforme Tr5%=1s Conforme | Ecart 1s Tr5%=2s
Premier dépassement inférieur à 4 mm quelle que soit l’amplitude de la consigne échelon | Non conforme Conforme D1=2.7 mm échelon 10mm ou 100 mm | Ecart du à la saturation

Correction : Asservissement en cap d’un pilote automatique de pénichette

Question : Il suffit d’écrire une seconde fois le même programme pour calculer d2.

// Programmation du capteur

digitalWrite(4, HIGH); //Broche Trig1 à l'état haut

delayMicroseconds(10); //on attend 10 µs

digitalWrite(4, LOW); //Broche Trig1 à l'état bas

duree1 = pulseIn(5, HIGH); // On lit la durée d’état haut sur la broche Echo1

if(duree1 < 30000) {d1=0.9*d1+0.1*duree1*345.0/2000000.0;}

digitalWrite(6, HIGH); //Broche Trig2 à l'état haut

delayMicroseconds(10); //on attend 10 µs

digitalWrite(6, LOW); //Broche Trig2 à l'état bas

duree2 = pulseIn(7, HIGH); // On lit la durée d’état haut sur la broche Echo2

if(duree2 < 30000) {d2=0.9*d2+0.1*duree2*345.0/2000000.0;}

d=(d1+d2)/2; // calcul de la distance moyenne

teta=(d2-d1)/0.404; // calcul du cap

Question : Kcap=200 donne des performances conformes au cahier des charges.

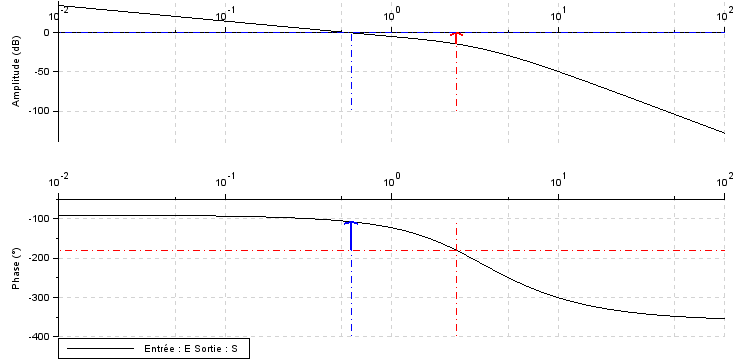
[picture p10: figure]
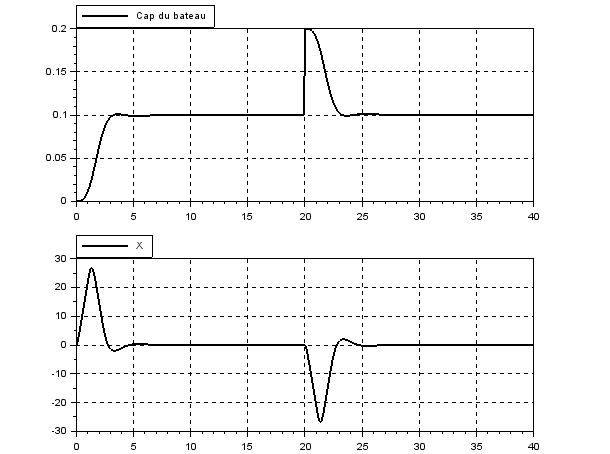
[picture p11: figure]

La saturation provoque l’instabilité de la réponse indicielle, mais comme elle n’est pas prise en compte dans le diagramme de Bode, ça ne se voit pas sur la marge de phase.

Question : Vérifiez le cahier des charges et déterminez les écarts entre les performances attendues, les performances simulées et les performances mesurées (remplir le tableau ci-dessous).

Performances attendues | Performances mesurées | Performances simulées
Ecart statique nul, même en présence de perturbations (tolérance ±0.01 rad) | Pas d’écart décelé Pas d’écart décelé Vérifié approximativement | Vérifié Pas d’écart décelé
Marge de phase Mφ≥50° | Conforme Pas d’écart décelé Le système semble stable | Pas d’écart décelé Mφ=73°
Temps de réponse à 5% inférieur à 12s pour une consigne en échelon de 0.1 rad | On a un petit dépassement a niveau de la barre mais par forcément au niveau de teta Conforme Le système rapide mais il faudrait le bateau pour vérifier Pas d’écart décelé Pas d’écart décelé | Pas d’écart décelé Pas d’écart décelé Tr5%=3s
Dépassement sur la réponse indicielle : 0 % | Conforme Pas d’écart décelé | Pas de dépassement

Correction : Asservissement en position d’un pilote automatique de pénichette

Question :

// Asservissement en position du pilote automatique

Cap=-Kpos*(dref-d);

Question : Si teta est petit, la vitesse d’éloignement de la rive est V*teta. Ensuite, on intègre pour avoir d.

Le vérin ne peut rentrer ou sortir que de 100 mm. Le longueur de la barre est e=360 mm.

Avec l’hypothèse teta petit, les saturations sont +Arcsin(100/360)≈+0.28 rad et - Arcsin(100/360)≈-0.28 rad

Kpos=0.3 donne un système conforme au cahier des charges.

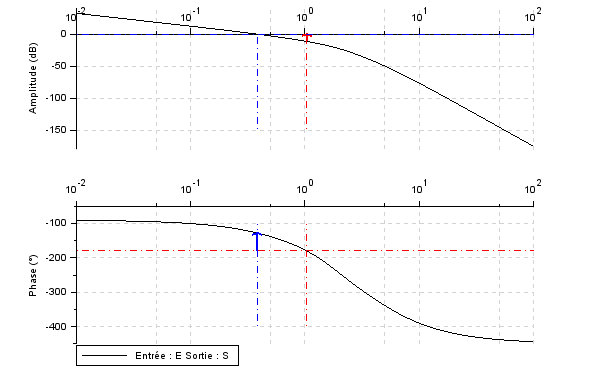
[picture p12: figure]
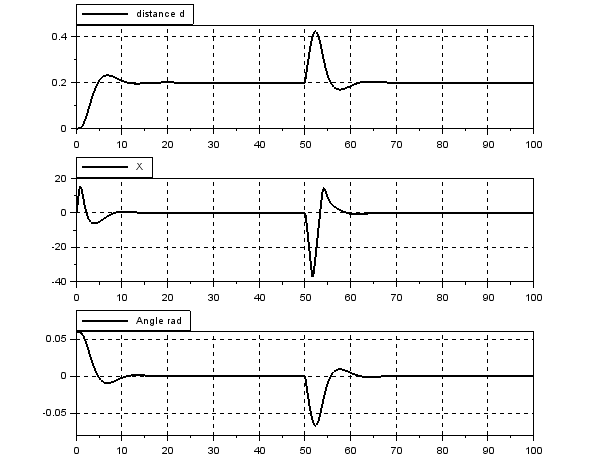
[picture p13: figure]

Question : Vérifiez le cahier des charges et déterminez les écarts entre les performances attendues et les performances simulées (remplir le tableau ci-dessous).

Performances attendues | Performances mesurées | Performances simulées
Ecart statique nul, même en présence de perturbations | | Ecart statique nul Vérifié
Marge de phase Mφ≥50° | Vérifié | Mφ=52°
Temps de réponse à 5% inférieur à 30s pour une consigne en échelon de 0.2 m | Vérifié | Tr5%=10 s
Dépassement sur la réponse indicielle < 20 % pour un échelon de 0.2 m | Vérifié | Dépassement 15%

Document1 Lycée Jean Mermoz 717 avenue Jean Mermoz, 34060 MONTPELLIER Cedex 2 08/01/2019

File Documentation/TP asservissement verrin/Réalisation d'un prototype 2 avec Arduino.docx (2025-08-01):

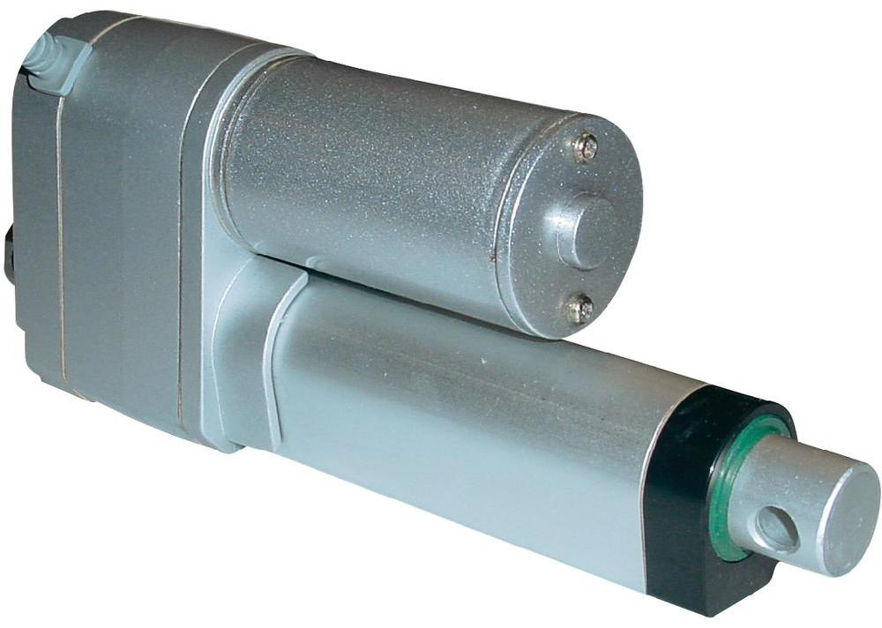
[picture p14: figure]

Réalisation d’un prototype

Première partie :

Vérin électrique asservi

Seconde partie :

Pilote automatique de péniche

Le travail s’effectue par îlots de 3 élèves :

- Un chef de projet qui coordonne le travail, récupère les résultats et rédige le compte rendu.
- Un expérimentateur qui programme la carte Arduino
- Un Modélisateur qui élabore les modèles Scilab et effectue le réglage du gain

# Compétences attendues

ANALYSER (S1-S2-S3)

DC1 Systèmes et informations | Architecture générale d'un produit · Analyse structurelle et comportementale ; · Chaîne d'information, chaîne d'énergie. | Analyser un système d’un point de vue structurel et comportemental
DC1 Systèmes et informations | Transmetteurs de puissance · Caractéristiques ; · Domaines d'application. | Analyser une solution de transmission de puissance
DC4 Systèmes linéaires continus invariants | Structure des systèmes asservis · Définition et structure d'un système asservi : chaîne directe (ou chaîne d'action), chaîne de retour (ou chaîne d'acquisition), comparateur et écart ; · Consigne, perturbation ; · Régulation, poursuite ; · Définition des performances : rapidité, précision et stabilité. | Justifier la nécessité d’un asservissement (analyse du couple performances/perturbations)
DC1 Systèmes et informations | Association de pré actionneurs et d’actionneurs · Caractéristiques ; · Domaines d'application. | Analyser une association de pré actionneurs et d'actionneurs
DC1 Systèmes et informations | Commandes programmables · Fonctions ; · Composants programmables. | Identifier les caractéristiques de la commande, E/S analogiques, numériques
DC1 Systèmes et informations | Description fonctionnelle des systèmes de traitement de l'information Architecture générale de la chaîne d'information. | Identifier et décrire les composants associés au traitement de l’information
DC1 Systèmes et informations | Information · Définition et nature, information et support d'information; · Information discrète (TOR et numérique), codage ; · Information analogique. | Identifier la nature et le support d’information
DC1 Systèmes et informations | Capteurs · Fonctions ; · Nature des grandeurs physiques d'entrées et de sorties; · Nature du signal, support de l’information. | Caractériser un capteur (grandeur physique observée et utilisable, transducteur)

MODELISER (S1,S3,S4)

DC4 Systèmes linéaires continus invariants | Systèmes linéaires continus et invariants · Modélisation par équations différentielles ; · Représentation par fonction de transfert (formalisme de Laplace) ; · Modèles canoniques 1er et 2ème ordre. | Identifier le comportement d’un système pour l’assimiler à un modèle canonique, à partir d’une réponse temporelle ou fréquentielle Établir un modèle de comportement à partir de relevés expérimentaux
DC4 Systèmes linéaires continus invariants | Systèmes linéaires continus invariants asservis · Représentation par schémabloc ; · Fonction de transfert en boucle ouverte et en boucle fermée ; · Classe d’un système. | Écrire un schéma bloc du système Déterminer les fonctions de transfert du système en boucle ouverte et en boucle fermée
DC4 Systèmes linéaires continus invariants | Systèmes non linéaires · Modèle de non linéarité (hystérésis, saturation, seuil, retard) ; · Linéarisation du comportement des systèmes non linéaires continus. | Identifier les non linéarités Identifier le point de fonctionnement pour la linéarisation du modèle du système non linéaire
DC4 Systèmes linéaires continus invariants | Modélisation des systèmes asservis · Stabilité : - définition, nature de l’instabilité (apériodique, oscillatoire), - contraintes technologiques engendrées, - interprétation dans le plan des pôles, - critère du revers, - marges de stabilité, - dépassement. | Caractériser la stabilité (marges de stabilité)
DC4 Systèmes linéaires continus invariants | Modélisation des systèmes asservis · Performances et réglages ; · Précision d’un système asservi en régime permanent pour une entrée en échelon, une entrée en rampe, une entrée en accélération ; · Rapidité d’un système asservi : - temps de réponse, - bande passante. | Justifier une simplification du modèle Déterminer l’influence du gain et de la classe de la fonction de transfert en boucle ouverte sur la précision et la rapidité
DC4 Systèmes linéaires continus invariants | Modélisation des systèmes asservis · Amélioration des performances d’un système asservi ; - critères graphiques de stabilité dans les plans de Black, Bode, marges de stabilité ; - influence et réglage d’une correction proportionnelle, intégrale, dérivée ; - prise en compte d’une perturbation constante, créneau ou sinusoïdale. | Mener une démarche de réglage d’un correcteur pour obtenir les performances attendues
DC4 Systèmes linéaires continus invariants | Systèmes asservis · Point de fonctionnement ; · Non-linéarités (hystérésis, saturation, seuil…). | Vérifier la cohérence du modèle choisi avec les résultats d’expérimentation ou/et de simulation

REALISER (S4)

DC8 ANALYSER CONCEVOIR et REALISER | Réalisation d’un prototype | Réaliser tout ou partie d’un prototype Valider l’architecture fonctionnelle et structurelle Valider les choix des composants vis-à-vis des performances attendues | L’acquisition de savoir-faire professionnels est exclue. On se limitera à : - réaliser une pièce prototype ; - implanter (alimenter, paramétrer) une carte de commande dans son environnement matériel ; - programmer à partir d’outils graphiques. Les langages de programmation ne donnent pas lieu à évaluation.

Vérin électrique asservi

Partie commune aux 3 élèves : Questions 1 à 4 et 14

Travail de l’expérimentateur : Questions 5 à 7

Travail du modélisateur : Questions 8 à 13

# Description du système et de sa commande

## Description de l’actionneur :

Il est animé par un petit moteur à courant continu, avec vis trapézoïdale et butées de fin de course. La vitesse peut être réduite par une diminution de la tension appliquée. La modification du sens se fait par permutation de la polarité. Un potentiomètre renvoie une tension proportionnelle à la longueur de tige sortie.

Caractéristiques techniques :

Fabricant N° | 16012114CR
Référence | DLA-12-10-A-200-POT-IP65
Démultiplication | 10:1
Indice de protection | IP65
Type | Vérin électrique
Spécificité | Avec potentiomètre intégré
Vitesse | 27 mm/s
Effort maximum | 250 N
Longueur de course | 200 mm
Tension nominale | 12 V/DC
Matériau | alliage en zinc (boîtier) et aluminium (tube extérieur et tige).

## Description de l’interface de puissance :

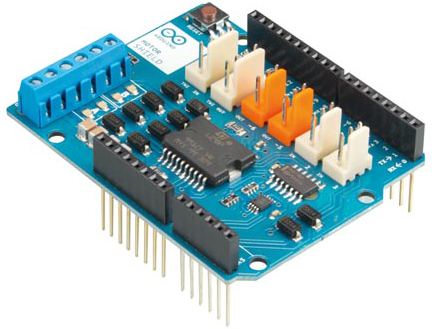
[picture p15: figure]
arduino® motor shield rev3

L’Arduino® motor shield rev3 est basé sur le L298, un double pont en H pour piloter des composants inductifs comme des moteurs à courant continu.

Ce shield a deux canaux séparés: A et B. Ils utilisent chacun 4 broches pour:

- le sens de rotation
- la vitesse de rotation
- le freinage rapide
- la mesure de la valeur absolue du courant dans le moteur

Vous pouvez utiliser chaque canal séparément pour alimenter deux moteurs à courant continu. Le shield peut fournir 2 ampères par canal, pour un total de 4 ampères au maximum.

Ce shield est directement enfiché sur une carte Arduino Uno, ce qui évite les câblages.

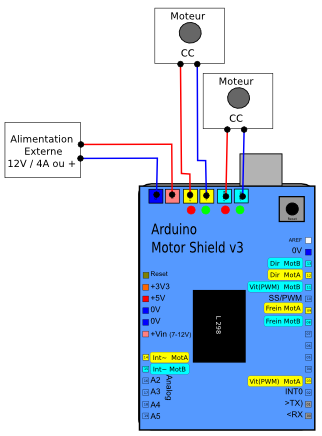
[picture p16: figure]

A

B

pin 13 Dir MotB

pin 12 Dir MotA

pin PWM 11 Vit MotB

pin 9 Frein MotA

pin 8 Frein MotB

pin analogique A0 Courant MotA

pin analogique A1 Courant MotB

pin PWM 3 Vit MotA

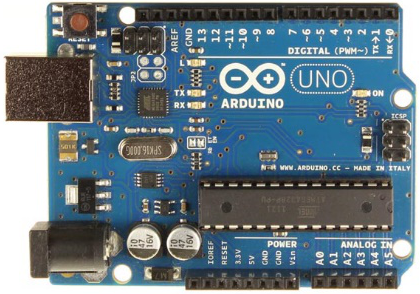
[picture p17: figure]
carte arduino uno rev 3

## Description de la partie commande :

Il s’agit d’une Arduino UNO.

Lancez le logiciel Arduino version 1.7.7 ou supérieure et connectez l’Arduino au port USB de l’ordinateur.

Cliquez :

Outils ; Type de carte ; Arduino/Genuino Uno

Outils ; Port ; et sélectionnez le port série sur lequel est connectée l’Arduino.

## Description des câblages :

La carte Motor Shield est alimentée par une alimentation externe 12V

Le moteur du vérin électrique est branché sur les bornes du moteur B

Le potentiomètre donnant la position de la tige du vérin est câblé de la façon suivante :

- fil jaune alimenté en 5V
- fil blanc est relié à GND (0V)
- fil bleu relié à A2

# Partie commune aux 3 élèves : Mise en œuvre du vérin

Objectifs de cette partie : Faire fonctionner l’actionneur dans les deux sens

Manipulation :

- Démontez l’actionneur de la maquette
- Copiez le programme Pilote_Auto_Vide dans votre espace de travail.
- Ouvrez ce fichier avec le logiciel Arduino version 1.7.7 ou supérieure.
- Enregistrez régulièrement votre travail en changeant le nom du fichier

Dans la partie 1 du programme sont définies toutes les variables.

Pour commencer, nous n’utiliserons que les variables vérin :

// Variables vérin

int Vit; //Vitesse moteur (Pin 11 0-255)

int Dir; //Sens rotation moteur (Pin 13 0-1)

int Pot_V; //Potentiomètre Vérin (Pin A2 0-1023)

int I; //Courant moteur (Pin A1 0-1023)

float IA; //Courant moteur (Ampères)

int IMax=1; //Courant Max moteur (Ampères) Ne pas dépasser cette valeur

int arretMot=0; //Demande d'arrêt moteur (0-1)

long temps=0; //Temps depuis début du programme (milli sec)

int signifie que la variable est un entier (integer)

long signifie que la variable est un entier de grande longueur (elle occupe plus de mémoire)

float signifie que la variable est un flottant (nombre avec virgule)

Dans la partie 2 du programme sont définies la vitesse de la sortie série (115200 baud ou bits/s) et le mode de fonctionnement des pins. Pour commencer, nous n’utiliserons que les pin 13 (sortie Dir) et 11 (sortie Vit)

Serial.begin(115200); // Initialisation du port série à la vitesse de 115200 baud

pinMode(13, OUTPUT); // initialise pin 13 comme sortie (Direction moteur)

pinMode(11, OUTPUT); // initialise pin 11 comme sortie (Vitesse moteur)

Dans la partie 3 se trouve le programme que nous allons taper. Il est divisée en rubriques.

La rubrique « Commande du moteur » est déjà programmée. Elle envoie la direction et la vitesse au moteur.

// Commande du moteur

if (arretMot==1 or millis()>60000) {Vit=0;} // Arrêt moteur si surcharge ou aprés 60s

digitalWrite(13,Dir); // Envoie du sens rotation moteur

analogWrite(11, min(abs(Vit),255)); // Envoie de la vitesse avec saturation à 255

A la fin du programme se trouve un tableau de bord qui affiche l’état de toutes les variables en temps réel.

Il est accessible en cliquant après avoir télé versé le programme avec le bouton .

Important : Régler la vitesse de la liaison série à 115200 bits/s et arrêter le défilement automatique dès que l’expérience est terminée. Remonter la barre de défilement (à droite) pour revenir à l’instant 0

Tapez les lignes suivantes dans la partie 3 du programme à la rubrique : // Asservissement en position du vérin

Dir=1;

Vit=200;

Allumez l’alimentation.

Télé versez le programme avec le bouton . Affichez le tableau de bord en cliquant

- La commande if (arretMot==1 or millis()>60000) {Vit=0;} //Arrêt moteur si surcharge ou après 60s arrête le moteur automatiquement après 60s ou si la variable arretMot est à 1
- La commande digitalWrite(13,Dir); envoie la valeur 0 ou 1 sur le pin 13 de l’Arduino, et la carte motor shield rev3 convertit cette valeur en une tension positive ou négative aux bornes du moteur (1=sortie de tige et 0=rentrée de tige).
- La commande analogWrite(11, min(abs(Vit),255)); envoie la valeur absolue de la variable Vit sur le pin PWM 11 de l’Arduino. Un valeur comprise entre 0 et 255 est convertit par la carte motor shield rev3 en une tension comprise entre 0 et 12V en valeur absolue.

Si Vit dépasse 255, on envoie 255. Cette non linéarité s’appelle la saturation.
Si Vit est trop faible, le moteur ne démarrera pas. Cette non linéarité s’appelle le seuil.

Donnez des valeur à Vit. Pensez à changer la valeur de Dir à chaque expérience.

Télé versez le programme avec le bouton .

Question :

Déterminez la tension de saturation du moteur.

Déterminez le seuil du moteur (valeur seuil de Vit et tension seuil du moteur).

La sortie du potentiomètre est branchée sur le pin A2 de la carte Arduino. Le convertisseur analogique numérique transforme une tension comprise entre 0 et 5V en un entier compris entre 0 et 1023.

Tapez la ligne suivante dans la partie 3 du programme à la rubrique : // Asservissement en position du vérin

Pot_V=analogRead(2);

Télé versez le programme avec le bouton . Affichez le tableau de bord en cliquant

Question : En faisant fonctionner le vérin à Vit=255, relevez les valeurs Pot_V_mini et Pot_V_maxi. Relevez la course du vérin en faisant le différence (tige sortie-tige rentrée)

On définit la variable X (position de la tige). Xmini=0 et Xmaxi=course

Tapez la ligne suivante dans la partie 3 du programme à la rubrique : // Asservissement en position du vérin

Utilisez vos propres valeurs numériques.

X=map(Pot_V, Pot_V_mini,Pot_V_maxi,Xmini,Xmaxi);

Télé versez le programme avec le bouton . Affichez le tableau de bord en cliquant

Attention, car la fonction map renvoie un entier. Pour plus de précision, tapez :

X=map(Pot_V, Pot_V_mini,Pot_V_maxi,Xmini,10*Xmaxi)/10.0;

Tapez bien 10.0 et pas 10, pour que la division donne un flottant. Sinon, ce sera un entier, avec une précision moins bonne.

Le potentiomètre du vérin est très précis, mais la numérisation engendre une erreur de quantification qui est le déplacement correspondant à la mesure brute d’un point.

Question : Quelle est l’erreur de quantification sur la position du vérin ?

En dessous du calcul de X, calculez Dir automatiquement avec la ligne suivante :

Dir=((Xref-X)>0); Explication : Dir=1 si Xref>X (test vrai) Dir=0 si Xref<X (test faux)

Testez le fonctionnement en entrant une valeur pour Xref : Xref=100 ;

Le vérin atteint la position Xref mais il est instable. Heureusement, un arrêt automatique est prévu après 60s.

Identification de la fonction de transfert du moteur

Sauvegardez le programme précédent puis télé versez le programme tollbox_arduino_V3 disponible sur le réseau dans le dossier :

CL_2PT\Ressources\TP Arduino

Lancez Scilab Xcos et construisez le modèle ci-dessous à partir des palettes « Arduino », « CPGE » et « Systèmes à temps continu » :

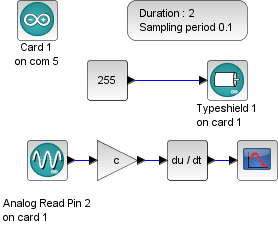
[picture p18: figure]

V (mm/s)

temps (s)

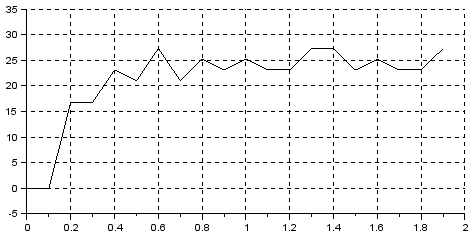
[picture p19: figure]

On envoie 255 à l’interface de puissance du moteur.

On lit le pin 2 (potentiomètre). « c » est le gain du potentiomètre qui transforme les points en mm

On dérive et on affiche le résultat en mm/s.

Cliquez sur Typeshield 1 et précisez bien qu’il s’agit du motor shield rev3 Moteur B.

Question : Identifiez la fonction de transfert du moteur. Donnez la valeur de son gain K avec unités et de sa constante de temps T. Donnez ces valeurs au modélisateur.

# Travail de l’expérimentateur

Vous pouvez ensuite fermer Scilab/Xcos et reprendre votre programme Arduino.

Pour stabiliser le vérin, il faut créer une boucle d’asservissement pour moduler la vitesse On choisit un correcteur proportionnel de gain Kp=10. Entrez cette valeur de Kp dans la partie 1 du programme.

En dessous du calcul de X, calculez Vit comme ci-dessous dans la partie 3 du programme à la rubrique :

// Asservissement en position du vérin

Vit=Kp*(Xref-X);

Entrez une autre valeur de Xref pour tester le fonctionnement.

Question :

- Pour quelles valeurs de se produisent la saturation et le seuil ?
- Faites des expériences pour déterminer l’écart statique de cet asservissement en position.
- D’où provient cet écart statique et comment peut-on la réduire ?

Filtrage du courant :

La mesure du courant peut se faire sur le pin A1 de l’Arduino et s’affiche sur le moniteur série.

Tapez la ligne suivante dans la partie 3 du programme à la rubrique : // Calcul du courant

I=analogRead(1);

Donnez une consigne et lisez la valeur brute du courant en points sur le tableau de bord. Vous remarquez qu’avant l’arrêt du vérin, le courant n’est pas stable du tout. Nous allons donc le filtrer avec un filtre passe-bas. Modifiez le calcul du courant avec la ligne suivante :

I=0.95*I+0.05*analogRead(1);

0.95*I signifie que l’on enlève 5% sur la valeur du courant précédent

+0.05*analogRead(1) signifie que l’on ajoute 5% de valeur fraiche au courant.

Ainsi, la valeur du courant se rafraîchit progressivement et les variations brusques du courant (hautes fréquences) n’interviennent que pour 5% de la valeur totale. Modifier en prenant les valeurs 0.9 et 0.1. Le rafraîchissement sera plus rapide mais le filtrage moins efficace. La somme doit toujours faire 1.

Nous allons maintenant calculer la valeur IA du courant en Ampères sachant que le gain du capteur de courant est de 1,65 V/A, et sachant que le convertisseur analogique-numérique de l’Arduino transforme 5V en 1023 points.

Question : Tapez une ligne de code pour calculer le courant IA en Ampères.

Testez le fonctionnement. Le courant doit être inférieur à 1A sauf lors des accélérations et décélérations.

Question : L’alimentation supporte une charge nominale de 3A, le moteur 2,3A et la carte Motor Shield v3 2A. Pour des raisons de sécurité, on décide de limiter le courant IMax à 1A (voir Imax dans la partie 1 du programme)

Dans la partie 3 du programme à la rubrique : // Programmation de l’arrêt moteur en cas de surcharge, écrivez la ligne suivante et faites des tests en bloquant manuellement la tige du vérin lors du déplacement :

if (IA>IMax) {arretMot=1;}

Vous pouvez reprendre le mouvement en appuyant sur la touche « Reset » de la carte Motor Shield v3.

Cette commande risque de nous poser des problèmes, car à chaque démarrage, le courant est fort et le moteur risque de s’arrêter aussitôt.

La fonction millis() donne le temps absolu en ms depuis le lancement du programme.

En écrivant temps=millis(); vous relevez l’instant présent dans la variable temps.

Modifiez la ligne de code ci-dessus pour couper la vitesse du moteur (arretMoteur=1) si le courant dépasse IMax=1A pendant plus de 500 ms consécutives. On éliminera ainsi les surcharges dues au démarrage.

Vérifiez le fonctionnement en bloquant manuellement la tige du vérin. Il doit s’arrêter en cas de surcharge.

Ce type de commande est souvent utilisé pour arrêter les moteurs électriques, par exemple pour les vitres électriques des voitures, qui s’arrêtent automatiquement en cas de blocage.

Pour la suite, pour éviter les arrêts du vérin, dans la partie 1 du programme, portez la valeur de IMax à 2A.

# Travail du modélisateur : Optimisation de la boucle d’asservissement

Cahier des charges :

- Ecart statique nul, même en présence de perturbations (tolérance ±0.2 mm)
- Marge de phase Mφ≥50°
- Temps de réponse à 5 % inférieur à 3s pour un échelon de 10 mm
- Premier dépassement inférieur à 4 mm quelle que soit l’amplitude de la consigne échelon

Objectif : Détermination des paramètres du correcteur PI par la méthode de l’optimum symétrique et simulation avec Scilab Xcos

Construire sous Scilab Xcos et la palette CPGE le schéma bloc de la boucle d’asservissement de position avec un correcteur proportionnel intégral de fonction de transfert :

s étant la variable de Laplace.

On note la constante de temps du correcteur.

L’entrée est un échelon de 10 mm

E et S se trouvent dans la palette CPGE/Analyses (grandeurs physiques)

Cliquez : Simulation ; Modifier le contexte et entrez les valeurs numériques des différents paramètres.

Prendre les valeurs Ki=10 et a=1 pour commencer l’étude.

Ki=10;

a=1;

T=_ma_constante_de_temps;

K=_mon_gain;

Question : D’après les expériences précédentes et d’après le cahier des charges, justifiez la présence d’un correcteur comportant une intégration.

Question : Montrez qu’il n’est pas possible d’utiliser un correcteur intégral pur de fonction de transfert .

Pour appuyer votre réponse, faites une simulation avec a=0.

Question : Montrez que « a » doit être plus grand que 1. Pour appuyer votre réponse, faites une simulation avec a=0,5.

Question : En faisant des simulations avec Scilab, déterminez la valeur de « a » qui donne une remontée de phase jusque -130°.

Question : En faisant des simulations avec Scilab, déterminez la valeur de « Ki » qui donne une marge de phase Mφ conforme au cahier des charges. Calculez la valeur de « Kp » et donnez les valeurs de « Kp » et « Ki » à l’expérimentateur.

Question : Le système réel comporte une non linéarité puisque l’Arduino motor shield rev 3 reçoit une consigne comprise entre -255 et +255. Modifiez le modèle Scilab en ajoutant cette non linéarité et vérifiez la conformité du modèle au cahier des charges pour un échelon de 10 mm puis pour un échelon de 100 mm.

# Travail commun et vérification expérimentale

Le correcteur proportionnel est déjà en place. Il reste à programmer le correcteur intégral.

Dans la partie 1 : // Variables asservissement en position du vérin, entrez vos valeurs de « Kp » et « Ki ».

Dans la partie 3 // Asservissement en position du vérin, ajoutez les lignes de code suivantes pour calculer (intégration par la méthode des rectangles).

tInt=micros(); // temps absolu depuis le démarrage de la carte (en µs)

if (abs(Vit)<=255) {integral=integral+(Xref-X)*((tInt-tIntPrec)/1000000);}

tIntPrec=tInt;

Dans notre cas, la période d’échantillonage Te=tInt-tIntPrec est recalculée à chaque boucle.

La bibliothèque SimpleTimer (pas utilisée ici) permet de définir une période d’échantillonnage constante.

Astuce : Il ne faut pas intégrer pendant la durée de la saturation, c'est-à-dire quand Vit>255, car le dépassement deviendrait très très important pour les grands échelons. Vous pouvez le vérifier dans le modèle Scilab avec saturation en donnant un échelon de 100 mm ou dans le programme Arduino en enlevant le test : if (abs(Vit)<=255)

Enfin, modifiez la ligne de code calculant Vit : Vit=Kp*(Xref-X)+Ki*integral;

Question : Vérifiez le cahier des charges et déterminez les écarts entre les performances attendues, les performances simulées et les performances mesurées.

Performances attendues | Performances mesurées | Performances simulées
Ecart statique nul, même en présence de perturbations (tolérance ±0.2 mm)
Marge de phase Mφ≥50°
Temps de réponse à 5 % inférieur à 3s pour un échelon de 10 mm
Premier dépassement inférieur à 4 mm quelle que soit l’amplitude de la consigne échelon

Asservissement en cap d’un pilote automatique de pénichette

Travail de l’expérimentateur : Questions 15

Travail du modélisateur : Questions 16

Partie commune aux 3 élèves : Question 17-18

Objectif : Créer un prototype fonctionnel de pilote automatique pour petite péniche asservi en cap.

Deux capteurs à ultrason situés sur les côtés de la péniche, au raz de l’eau mesurent l’angle θ entre la péniche et la berge du canal. Un asservissement permettra de maintenir cet angle égal à la consigne définie par le timonier.

Cette consigne est le Cap. Logiquement, il faudrait Cap=0 pour rester parallèle aux berges du canal.

Hypothèses :

Les angles seront considérés petits.

La péniche se déplace à la vitesse V=5 km/h=1.39 m/s

La fonction de transfert de la péniche est : avec s la variable de Laplacec

Justification : si l’on incline la barre de α=0.1 rad (5.7°) à la vitesse V=5 km/h, la pénichette tourne à la vitesse (soit un tour en 1 minute), avec un temps de réponse de 3×0.5s.

Berge du canal

Barre

Capteur à ultrasons 2

Capteur à ultrasons 1

d2

d1

e

b

Pilote

automatique

Vitesse V

X

α

θ

# Travail de l’expérimentateur

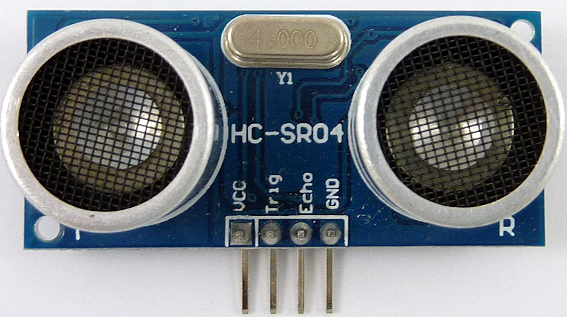
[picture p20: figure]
Résultat de recherche d'images pour "capteur à ultrasons"

## Mise en œuvre des capteurs à ultrasons :

A part son alimentation 5V (broche VCC) et la masse (broche GND), le capteur à ultrasons fonctionne à partir des deux pins Trig et Echo, qui doivent être connectés à deux pins d’un microcontrôleur Arduino.

Capteur à ultrasons 1 : Trig1 relié au pin 4 Echo1 relié au pin 5 | Capteur à ultrasons 2 : Trig2 relié au pin 6 Echo2 relié au pin 7

- La demande de la mesure s’effectue en maintenant la broche Trig à l’état 1 pendant 10 µs.
- Le capteur émet alors de courtes impulsions sonores à haute fréquence. Ces impulsions se propagent dans l’air à la vitesse du son (345 m/s). Lorsqu’elles rencontrent un objet, elles se réfléchissent et reviennent sous forme d’écho au capteur. Celui-ci calcule alors la distance le séparant de la cible sur la base du temps écoulé entre l’émission du signal et la réception de l’écho.
- Le capteur donne le résultat de sa mesure en maintenant la broche Echo à l’état 1 pendant le temps qu’à mis le son pour aller jusqu’à la cible et revenir. Le cycle dure un peu plus de 60ms, soit une fréquence de rafraichissement de 16 Hz environ.

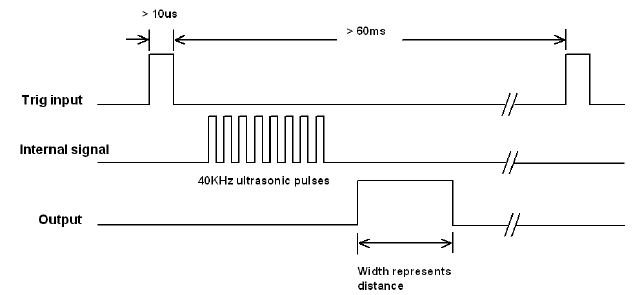
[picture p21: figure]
Résultat de recherche d'images pour "capteur à ultrasons"

durée

Largeur représentant la distance

Impulsions ultrason à 40 kHz

Signal interne

Echo

Trig

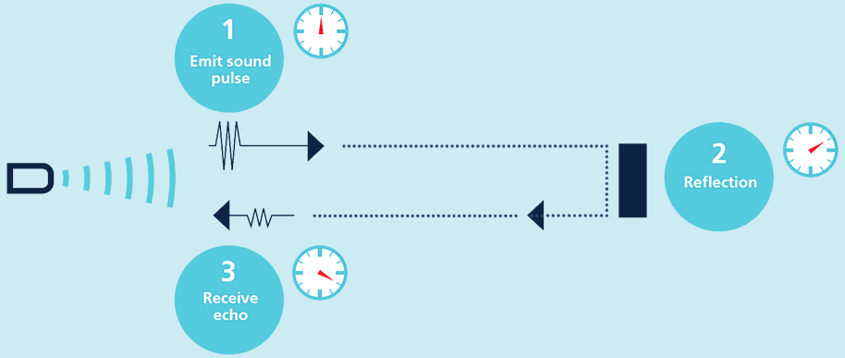
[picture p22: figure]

Les capteurs à ultrasons microsonic détectent tout type d’objet et sont disponibles pour des portées de 20 mm à 10 m et, du fait même de leur principe, donnent la valeur mesurée au millimètre près.

Lancez le logiciel Arduino version 1.7.7 ou supérieure et connectez l’Arduino au port USB de l’ordinateur.

Ouvrez le fichier Pilote_Auto2_Verin

Ce fichier comporte l’asservissement en position du vérin fait dans le TP précédant.

Cliquez :

Outils ; Type de carte ; Arduino/Genuino Uno

Outils ; Port ; et sélectionnez le port série sur lequel est connectée l’Arduino.

Dans la partie 1 du programme se trouvent les // Variables capteur :

unsigned long duree1=0; // Temps aller-retour capteur 1/rive (micro sec)

unsigned long duree2=0; // Temps aller-retour capteur 2/rive (micro sec)

float d1=0; // Distance capteur 1/rive (métres)

float d2=0; // Distance capteur 2/rive (métres)

float d=0; // Distance péniche/rive (métres)

float teta=0; // Cap péniche/rive (rad)

Dans la partie 2 du programme, on a initialisé les pins des capteurs :

pinMode(4, OUTPUT); // Initialise pin 4 comme sortie (Trig 1)

pinMode(5, INPUT); // Initialise pin 5 comme entrée (Echo 1)

pinMode(6, OUTPUT); // Initialise pin 6 comme sortie (Trig 2)

pinMode(7, INPUT); // Initialise pin 7 comme entrée (Echo 2)

Dans la partie 3 du programme à la rubrique : // Programmation du capteur, écrivez (sans les commentaires) :

digitalWrite(4, HIGH); //Broche Trig1 à l'état haut

delayMicroseconds(10); //on attend 10 µs

digitalWrite(4, LOW); //Broche Trig1 à l'état bas

// On lit la durée d’état haut sur la broche Echo1 en micro secondes

duree1 = pulseIn(5, HIGH);

//d1 est filtrée aves 90% de valeurs anciennes et 10% de valeurs fraiches

//si durée1 > 30000 micro secondes, l'onde est perdue

if(duree1 < 30000) {d1=0.9*d1+0.1*duree1*345.0/2000000.0;}

//on multiplie par la vitesse, d1=duree1*v/2

Attention, car duree1 est un entier. Tapez bien 345.0 pour obtenir un flottant. Sinon, d1 sera toujours nulle.

Téléversez le programme avec le bouton . Affichez le tableau de bord en cliquant .

Placez l’écran à 20 centimètres du capteur et vérifiez que la mesure de d1 est juste. Eventuellement, vous pouvez ajuster la célérité du son pour obtenir un résultat plus précis (355 à la place de 345 m/s)

Question : Elaborez un programme qui renvoie l’angle teta=(d2-d1)/b (avec l’hypothèse d’angle petit) et la distance moyenne d=(d1+d2)/2. Mesurez b sur la maquette. Testez le fonctionnement.

# Travail du modélisateur

Objectif : Déterminer le gain du correcteur de la boucle d’asservissement en cap.

Ouvrez le fichier « Modèle Vérin élec.zcos » qui contient la correction du TP Vérin électrique Asservi.

A partir du modèle Scilab Xcos non linéaire du vérin électrique asservi en position, réalisez le modèle ci-dessous de l’asservissement en Cap (c'est-à-dire de l’asservissement angulaire).

La consigne est un échelon, instant 0, valeur initiale 0, valeur finale 0.1 rad.

La perturbation est un échelon, instant 20s, valeur initiale 0, valeur finale 0.1 rad.

Cliquez : Simulation ; Modifier le contexte et entrez les valeurs de Kcap et e :

Kcap=1000 ;

e= 360mm ; (longueur de la barre, voir page 11)

Cahier des charges :

- Ecart statique nul, même en présence de perturbations (tolérance ±0.01 rad)
- Marge de phase : Mφ≥50°
- Temps de réponse à 5% inférieur à 12s pour une consigne en échelon de 0.1 rad
- Dépassement sur la réponse indicielle < 5%

Question :

- En faisant des simulations successives, déterminez la plus grande valeur de Kcap qui donne des performances conformes au cahier des charges.
- Comment expliquez-vous que certaines valeurs de Kcap donnent un comportement instable sur la réponse indicielle et stable sur le diagramme de Bode ?

# Travail commun aux 3 élèves

Entrez votre valeur de Kcap dans la partie 1 du programme Arduino à la rubrique :

// Variables asservissement en cap du pilote automatique

Tapez dans la partie 3 du programme à la rubrique // Asservissement en cap du pilote automatique

Cap=0 ; //pour demander un déplacement parallèle à la berge

Xref=100-Kcap*(Cap-teta) ; //pour que le vérin soit en position centrale (X=100) quand Cap=teta

Téléversez le programme avec le bouton . Affichez le tableau de bord en cliquant .

Testez le fonctionnement. Quand la barre tourne, vous devez tourner le réflecteur pour simuler le mouvement de la pénichette.

Question : Vérifiez le cahier des charges et déterminez les écarts entre les performances attendues, les performances simulées et les performances mesurées (remplir le tableau ci-dessous).

Performances attendues | Performances mesurées | Performances simulées
Ecart statique nul, même en présence de perturbations (tolérance ±0.01 rad)
Marge de phase Mφ≥50°
Temps de réponse à 5% inférieur à 12s pour une consigne en échelon de 0.1 rad
Dépassement sur la réponse indicielle : 0 %

Asservissement en position d’un pilote automatique de pénichette

Travail de l’expérimentateur : Questions 18

Travail du modélisateur : Questions 19

Partie commune aux 3 élèves : Question 20

Objectif : Créer un prototype fonctionnel de pilote automatique pour petite péniche asservi en position.

Deux capteurs à ultrason situés sur les côtés de la péniche, au raz de l’eau mesurent la distance d et l’angle θ entre la péniche et la berge du canal. Un asservissement permettra de maintenir cette distance d égale à la consigne dref=0.2 mètres.

Hypothèses :

Les angles seront considérés petits.

La péniche se déplace à la vitesse V=5 km/h=1.39 m/s

La fonction de transfert de la péniche est : avec s la variable de Laplacec

Justification : si l’on incline la barre de α=0.1 rad (5.7°) à la vitesse V=5 km/h, la pénichette tourne à la vitesse (soit un tour en 1 minute), avec un temps de réponse de 3×0.5s.

Berge du canal

Barre

Capteur à ultrasons 2

Capteur à ultrasons 1

d2

d1

e

b

Pilote

automatique

Vitesse V

X

α

θ

# Travail de l’expérimentateur

Le timonier donne comme consigne la distance par rapport à la berge : dref=0.2 mètres

Dans la partie 1 du programme, on trouve les différentes variables :

// Variables asservissement en position du pilote automatique

float dref=0.2; //Consigne de position (mètres)

float Kpos=1; //Gain correcteur de position

Dans la partie 3 du programme, rubrique // Asservissement en cap du pilote automatique

Effacer la ligne Cap=0 ; car la cap va être calculé automatiquement

Question :

Tapez dans la partie 3 du programme, rubrique // Asservissement en position du pilote automat

Cap=-Kpos*( ?????????);// Le signe – peut être nécessaire si la barre se déplace dans le mauvais sens

Testez le fonctionnement en déplaçant l’écran réflecteur. Vérifiez que le bateau se stabilise à dref=0.2 mètres de cet écran.

# Travail du modélisateur

Cahier des charges :

- Ecart statique nul, même en présence de perturbations
- Marge de phase : Mφ≥50°
- Temps de réponse à 5% inférieur à 30s pour une consigne en échelon de 0.2 m
- Dépassement sur la réponse indicielle : <20 % pour un échelon de 0.2 m

Question : A partir du modèle Scilab Xcos de l’asservissement en cap, réalisez le modèle de l’asservissement de position. Déterminez les valeurs des saturations en cap (voir ci-dessous).

En faisant des simulations successives, déterminez la plus grande valeur du correcteur proportionnel Kpos pour que le système soit conforme au cahier des charges.

# Travail commun aux 3 élèves

Question : Pour mieux visualiser le fonctionnement, conservez la valeur Kpos=1 sur la maquette. Vérifiez le cahier des charges et déterminez les écarts entre les performances attendues et les performances simulées (remplir le tableau ci-dessous).

Performances attendues | Performances mesurées | Performances simulées
Ecart statique nul, même en présence de perturbations
Marge de phase Mφ≥50°
Temps de réponse à 5% inférieur à 30s pour une consigne en échelon de 0.2 m
Dépassement sur la réponse indicielle : <20 % pour un échelon de 0.2 m

Réalisation d'un prototype 2 avec Arduino.docx Lycée Jean Mermoz 717 avenue Jean Mermoz, 34060 MONTPELLIER Cedex 2 08/01/2019

PT DC8- REALISER : Réalisation d’un prototype p 9

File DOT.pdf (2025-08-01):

Mars 2023: Choix du sujet. Recherche sur les solutions utilisés par les participants de la Robocup. Recherche sur la mécanique et la conception des robots holonomes.

Mai 2023 : Achats des premiers composants et début des tests de montages électriques. Apprentissage du contrôle d’un moteur avec un Arduino et l’utilisation de codeurs incrémentaux. Réalisation d’une première étude théorique permettant de vérifier la faisabilité d’un robot holonome.

Juin 2023 : Premier assemblage du robot et premier programme informatique complet. Premier essai qui s’est soldé par un échec, les moteurs n’arrivaient pas à déplacer le robot.

Septembre 2023 : Réception de nouveaux composants. Apprentissage du fonctionnement du nouveau driver moteur. Mise en place d’une nouvelle étude théorique, la première étude de Mai 2023 ne permettant pas de commander les moteurs.

Décembre 2023 : Choix du montage électrique final. Approfondissement de l’étude théorique à fin d’avoir une relation la plus générale possible.

Février 2024 : Assemblage final du robot et début des tests pour choisir l’étude expérimentale. Finalisation de l’étude théorique.

Mai 2024 : Une anomalie se déclare sur des moteur, devenant de fait inutilisable. Choix d’un nouvelle expérimentation plus simple mais réalisable.

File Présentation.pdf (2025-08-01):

# Robot

1

# Sommaire

2

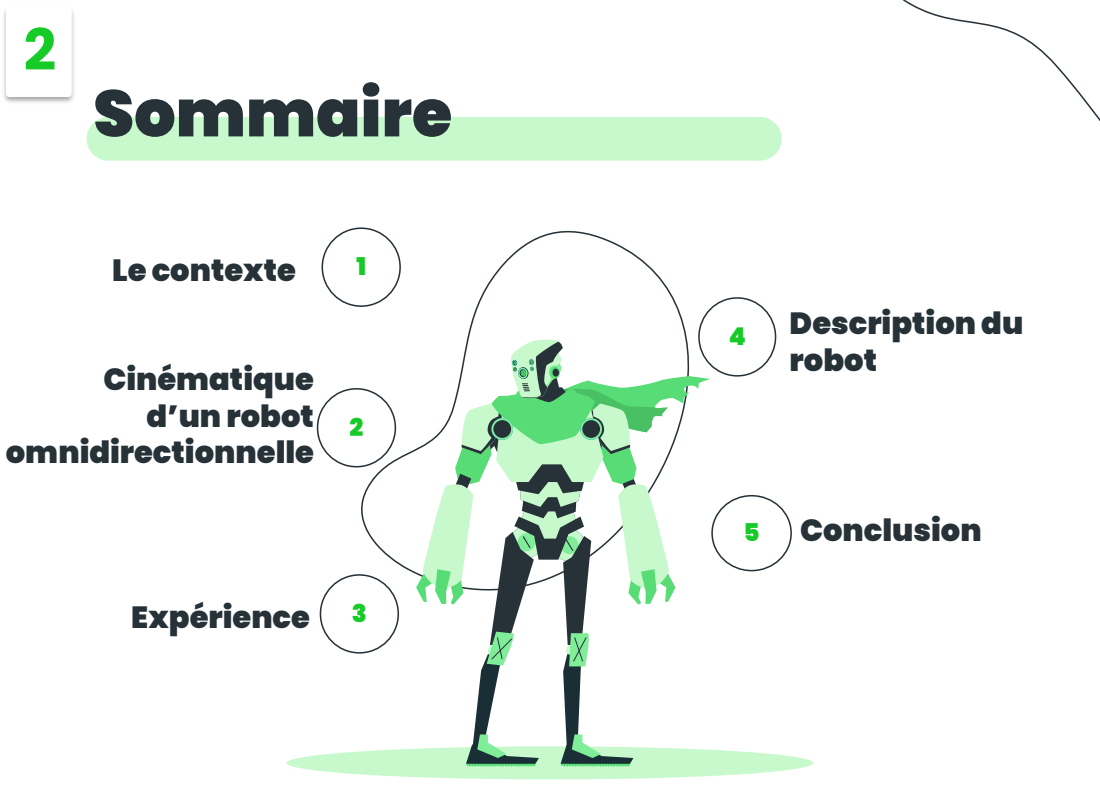
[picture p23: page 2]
Le contexte; Cinématique d’un robot omnidirectionnelle; Expérience 3; Description du robot; 5 Conclusion

# Le contexte

3

Références : https://www.iceberg-robots.de/2019/08/27/robocup-german-open-2019/ ; https://robocuprussiaopen.ru/en/events/russiaopen/2019/

# Problématique

5

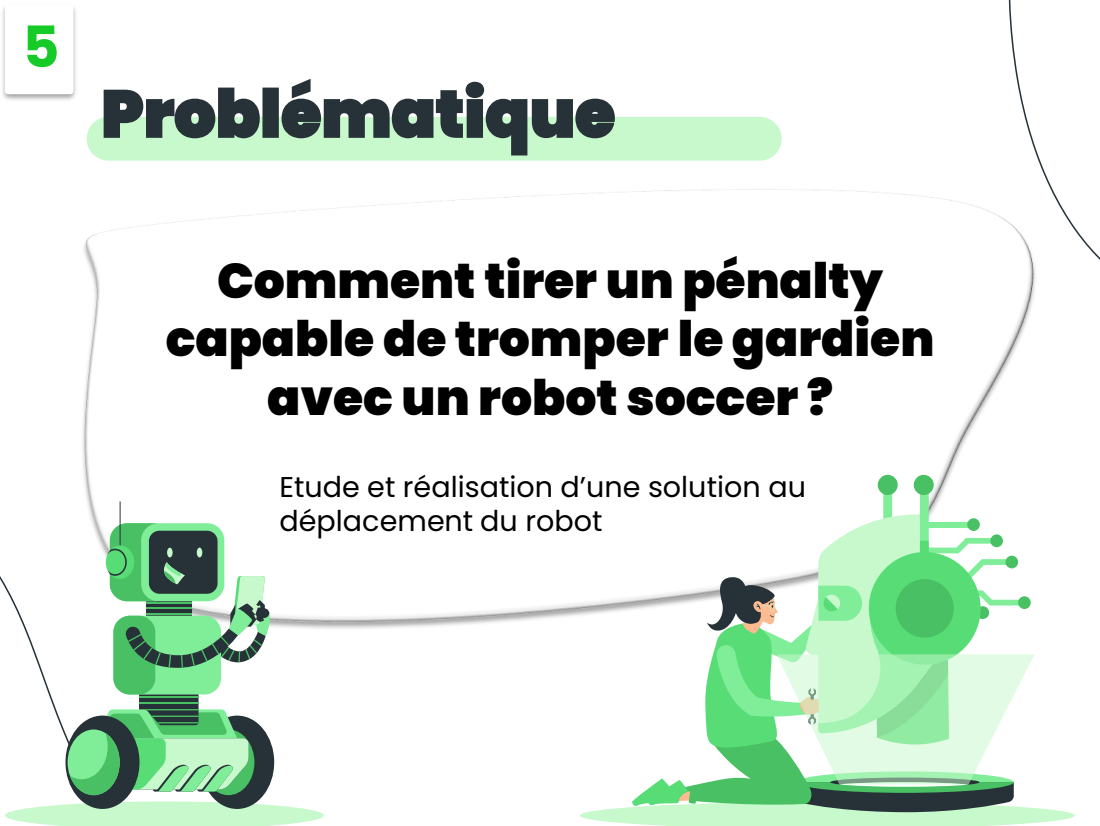
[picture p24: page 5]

Comment tirer un pénalty
capable de tromper le gardien
avec un robot soccer ?

Etude et réalisation d’une solution au
déplacement du robot

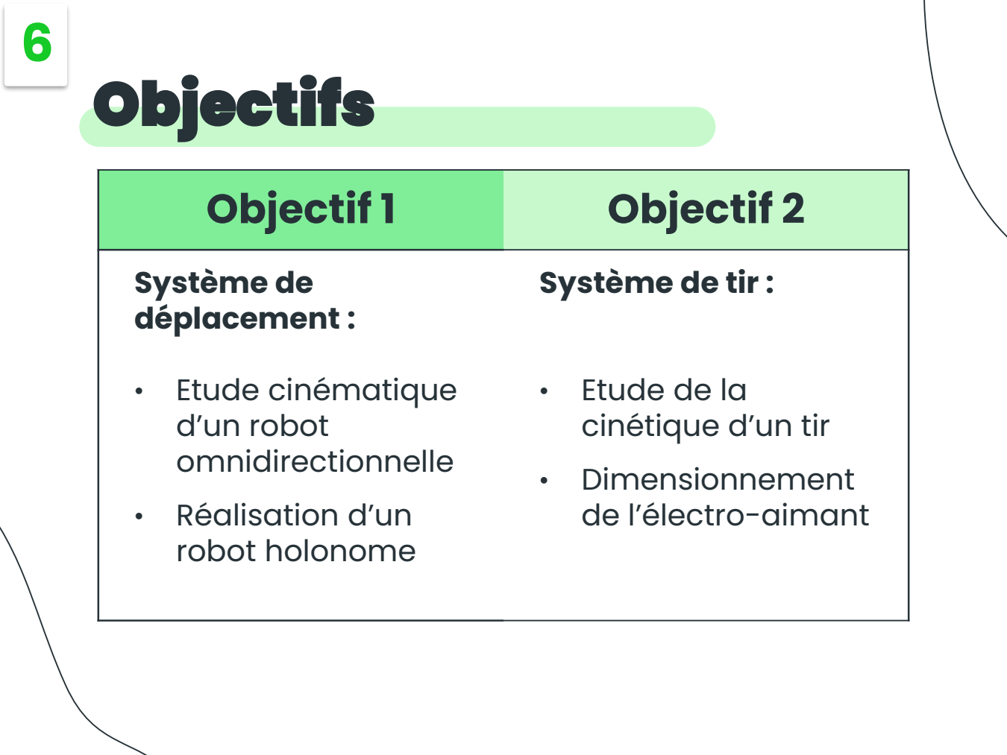
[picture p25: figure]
Objectif 1; Objectif 2; Système de déplacement :; • Etude cinématique d’un robot omnidirectionnelle • Réalisation d’un robot holonome; Système de tir :; • Etude de la cinétique d’un tir • Dimensionnement de l’électro-aimant; Objectifs

7

Objectif de l’étude :
Déterminer la relation entre la
vitesse du robot et la vitesse de
rotation des moteurs

# Paramétrage

8

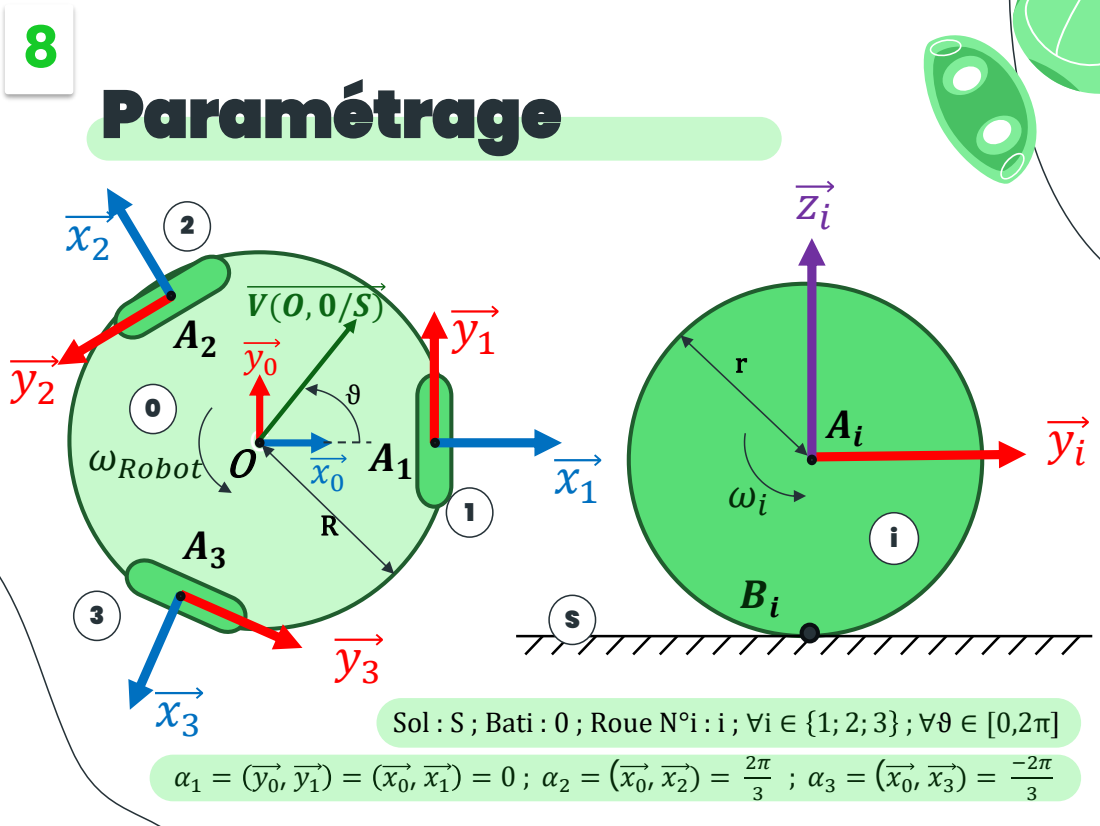
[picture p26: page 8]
ωRobot

Sol : S ; Bati : 0 ; Roue N°i : i ; ∀ⅈ ∈ 1; 2; 3 ; ∀ϑ ∈ [0,2π]

# Hypothèses

9

• Robot en translation plane et en rotation sur z0
• Largeur de la roue négligée, roue circulaire

# Calculs

10

, 0/S) = V(O, 0/S) + AiO Λ Ω0/S; , i/S) + BiAi Λ Ωi/S

• (1) et (2) : Formule de Varignon (Changement de point)

• Ai et Bi appartⅈennent à la roue ⅈ

# Calculs

11

# Calculs

12


Il suit que :

# Calculs

13

• Roue i en RSG selon yi

⟺ − u0/s sⅈn αi + v0/s cos αi + R ω0/s + r ωi = 0

u0/s sin αi − v0/S cos αi − R ω0/s

14

Expérience

Objectif de l ’expérience :
Tester la validité de la relation
établie par l’étude théorique

u0/s sin αi − v0/S cos αi − R ω0/s

# Protocole et hypothèse

15

• vRobot/Sol =; VO,0/S = vRobot x2

Hypothèses :
• Roulement sans glissement
• Baisse de tension de la batterie négligé

Protocole :
• Faire translater le robot selon x2
durant T secondes
• Mesurer L : la distance parcourut
• Mesurer ω1 et ω3 les vitesses de
rotation des roues 1 et 3 par
tracking vidéo

# Résultats théorique

16

u0/s sin αi − v0/S cos αi − R ω0/s

# Résultats pratique

Calcul des vitesses de déplacement du robot

Calcul des vitesses de déplacement du robot

Calcul des vitesses de rotation des roues

Vitesse de rotation à vide mesurée par tracking vidéo :

# Conclusion expérience

- D’importantes incertitudes
- Mesure des distances ≈ 1cm
- Vitesse de rotation mesurée à vide
- Forte influence du revêtement : augmentation de 35% de vitesse sur le carrelage par rapport au stratifié
- Problèmes électroniques
- Taux d’erreur :
- Meilleur cas : 21,9% (expérience 2)
- Pire cas : 42,4% (expérience 1)
- Conclusion et Axe d’amélioration : Taux d’erreurs importants à cause du glissement et de la mesure de vitesse de rotation mais modèle théorique validé. Par ailleurs, des amélioration sont à prévoir sur le prototype.

# Description

20

du Robot

• Les besoins
• Exigence de
déplacement
• Exigences du
règlement
• BDD
• Système de tir

# Les besoins

21

Rapidité
Compliquer la
tache du gardien

Respect du
Règlement
Avoir un robot crédible
pour participer à la
compétition

# Exigences de déplacement

22


# Exigences du règlement ²³

# Diagramme de définition de bloc 24


# Système de tir

25

- Electro-aimant à
solénoïde
- Certitude d’un tir cadré à une distance de
40cm
- Relation entre la
position de la frappe
sur la balle et la
position de la balle
dans les cages

# Solution problématique ²⁶

- Robot à roue omnidirectionnelles
- Liaison Robot/Sol ⟺ Liaison plan (CDC)
- Loi de commande des moteurs
- Vitesse max
- théorique : 770 mm/s > 500 mm/s (CDC)
- Expérimentale : 367 mm/s < 500mm/s (CDC)
- Système de tir fonctionnel
- Améliorations nécessaires :
- Montage électrique
- Raquette de tir

27

Merci pour votre attention

# Les problèmes

### Chaine de

puissance

Moteur
● Importants efforts
internes anormaux
● Anomalie absente
des autres moteurs
● S’est déclaré après
assemblage

● Tout les moteurs
tournent bien à vide
● Difficile de solliciter
plusieurs moteurs en
même temps
● Ne tournent plus une
fois chargé

# Problème : Chaine de puissance

Driver L9910; Courant max : 2 Ampère; Breadboard et fils arduino; Courant max : 1 Ampère; Abaisseur de tension; Courant max : 1,2 Ampère; Batterie • Capacité : 2,2Ah • Courant de décharge 50C ⇒ 110A; 3 Moteurs; • Consommation 1 moteur bloqué : 5,5 Ampère

max en
continu

Références : (Batterie) https://rcsearch.info/-c11374 ; (Abaisseur de tension L7806) https://thaipick.com/product/lazada/2221014 ; (Fil électrique Arduino) https://udvabony.com/product/male-to-female-jumper-wire-single/ ; (Breadboard) https://cukii.com/product/quality-solderless-breadboard-400-tie-point-pcb-breadboard-for-arduino-interconnect-any-components-with-20-29-awg-(0.3-0.8)-wire ; (Moteur) https://www.gotronic.fr/art-motoreducteur-34-1-encodeur-rs003-24295.html

30

# Solution : Chaine de puissance

max en
continu

Références : (Batterie) https://rcsearch.info/-c11374 ; (Abaisseur de tension) https://www.alibaba.com/product-detail/Factory-Tobsun-12v-24v-To-5v_1600627269932.html ; (Fil électrique) https://udvabony.com/product/male-to-female-jumper-wire-single/ ; (Breadboard) https://cukii.com/product/quality-solderless-breadboard-400-tie-point-pcb-breadboard-for-arduino-interconnect-any-components-with-20-29-awg-(0.3-0.8)-wire ; (Moteur) https://www.gotronic.fr/art-motoreducteur-34-1-encodeur-rs003-24295.html

31

# Diagramme des cas d’utilisation

Borne -; Borne +; Arduino Mega; Abaisseur de tension

Driver 1 (Moteur 1 et Moteur 2)

Interrupteur

Driver 1
(Moteur 3)

# Robot « omni »

### Avantages Inconvénients

- Liberté de
déplacement
- Maniabilité
- Vibration
- Manque
d’adhérence
- Besoin d’un couple
plus important
qu’un système
“classique”
- Système plus
complexe

# Robot « omni »


Configuration 3WD | Configuration 4WD

Référence : https://www.aliexpress.com/item/MT200S-4WD-100mm-Omni-Wheels-Robot-Car-Chassis-Stainsteel-Frame-Big-Power-Motor-For-DIY-Toy/32841507269.html

# Robot « omni »

3 roues motrices | 4 roues motrices
- + Stable :
- 3 points ⇒ 1 plan
- - Code plus complexe :
- Cinématique moins intuitive
- Mécanisme + simple :
- Chaines de puissance et
d’information plus légères
- Plus compact
| ● + d’adhérence ● + de couple ● Code + simple ● - Mécanisme plus complexe :
- Problème de planéité
- 4 moteurs à contrôler
- Encombrement plus important

Choix : Robot 3 roues motrices Critères retenus :
- Compacité
- Stabilité
- Simplicité de conception

# Omniwheel

Références : https://www.omnitrack.com/product-category/wheels-castors/omniwheels/ ; https://www.artstation.com/marketplace/p/rPw2/3d-mecanum-wheel ; https://tdp.robocup.org/wp-content/uploads/tdp/robocup/2021/robocupsoccer-small-size/ubc-thunderbots-273/robocup-2021-robocupsoccer-small-size-ubc-thunderbotsXRkqMjK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

Roue « mécanum »

Déplacement holonome; Configuration 3WD; Configuration 4WD

# Dessin support driver et moteur

Support driver | Support moteur

# Dessin support driver et moteur

Chassie moteur | Chassie supérieur

# Calcul expérience :

• vRobot/Sol =; VO,0/S = vRobot x2; = vRobot ( cos; x0 + sⅈn ²π; vRobot x0; vRobot y0; Alors :; vRobot; Nota bene :

1 ⇒ VO,0/S = vRobot ( cos α2 x0 + sⅈn α2 y0 )

Calcul expérience : ω1; Nota bene :; • Rayon roue : r = 29mm; • Relation : ωi =; u0/s sin αi − v0/S cos αi − R ω0/s; vRobot; Alors,; vRobot sⅈn 0 −; vRobot cos 0 )

# Calcul résultat pratique

# Expérience validation vidéo


- Faire tourner les moteurs à vide aux même consigne que durant l’expérience
- Mesure de temps pour 1 tour
- ω =

2π

T1 tour

=

2π
0,43

= 14,61 rad/s

# Expérience encodeur

1 moteur | 2 moteurs
- T1 = 0,27s ● Vitesse mesuré : 23 rad/s | ● T1 = 0,29s
| ● Vitesse mesuré : 11,55 rad/s

Calcul des vitesses de rotations

ω1mot =

2π
0,27 = 23,7 rad/s v2mot =

2π
0,29 = 21,66 rad/s

Conclusion

Mesure de l’encodeur
validé

Mesure de l’encodeur
invalidé



Ainsi, vO/S =; ,i/R0) + BiAiO Λ Ωi/S; Relation : ωi; vRobot

u0/s sin αi − v0/S cos αi − R ω0/s

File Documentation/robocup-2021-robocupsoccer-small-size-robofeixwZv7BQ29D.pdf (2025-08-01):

## RoboFEI 2020 Team Description Paper

Leonardo da S. Costa, Wesley de S. Motta, Danilo Pilotto, Guilherme L. Pauli, Jo˜ao V. L. Aguiar, Gabriel M. Schiavetto, Bruno Bollos Correa, Mateus Mariano Lucatelli, Marcos A. P. Laureano, Reinaldo A. C. Bianchi, Pl´ınio Thomaz Aquino Junior, and Flavio Tonidandel

Robotics and Artificial Intelligence Laboratory Centro Universit´ario da FEI, S˜ao Bernardo do Campo, Brazil {flaviot, rbianchi, plinio.aquino}@fei.edu.br

Abstract. This paper presents the current state of the RoboFEI Small Size League team as it stands for RoboCup International Small Size League competition 2020, in Bordeaux, France. The paper contains descriptions of the new electronic board design, a new modeling technique for the robots as well as a new position controller.

### 1 Introduction

For RoboCup 2020, the RoboFEI team intends to use mostly the same electronics and mechanical design that have been used over the last years. However, there are plans to test the new robot design, the mechanics are already described in last year TDP [8].
Some significant advances were made in our software, the improvements were verified in the XVIII Latin American Robotics Competition (LARC), which resulted in our seventh first place trophy. The objective now is to improve furthermore the software system and start replacing our current robots. With our researches, we hope to bring innovations and new ideas for the community.

### 2 Electronics

Restructuring the electronic boards using a modular structure has been the goal since RoboCup 2019. Each function will be arranged on a smaller board and all blocks will communicate over connections through a main board. This change aims to facilitate the maintenance of the robot. When identifying a problem, the faulty module will be replaced and separated for further analysis.
The first prototypes are being produced for RoboCup 2020. As soon as the new boards work properly, the old ones should be quickly replaced.

### 2.1 Modular Structure

Compared to the current structure, where the whole electronics are divided into a main, kick and radio boards, in the new structure there are nine modules.

These modules consists of five motor, one kick, one main, one radio and one STM32F407 Discovery boards. The block diagram representing these modules can be seen on Figure 1.


Fig. 1. New electronic board diagram.

### 2.2 Kick Board

The new kick board works with the Flyback topology based on the IC LT3751, the choice of this controller model was due to the possibility of checking the input voltage and defining an operating range, making it safer for the batteries. The system uses a 4000µF/200V capacitor. For the kick activation, it uses the IXFA56N30X3 MOSFET, which supports 300V and 56A. The board can control up to three solenoids.
For the capacitor, solenoids, battery and main board communication we use the connectors WM18823, WM4624, WM4300 and M20-9980445, respectively. The board model can be seen on Figure 2.


Fig. 2. New kick board.

### 2.3 Motor Board

Composed of the IC A4915 in conjunction with the IRF8313TRPBF MOSFET, the board receives a PWM signal for the motor and is responsible for controlling its speed using the input and feedback from all hall sensors.
The connector of choice for connecting the motor and main boards is the SAM11451 due to its robustness, which will be verified in the first prototypes. The board model can be seen on Figure 3.


Fig. 3. New motor board.

### 2.4 Main Board

Responsible for connecting all modules and performing the power and regulation necessary for the operation of each board and peripherals. The power will be carried through two 14, 8V batteries with a capacity of 1300mAh for better arrangement inside the robot. The supply voltage goes through a 5V buck regulator that will be distributed throughout the board.
To avoid connection issues with the encoder connectors, which were very present in our current main board, we are using the WM18921 connectors. For the battery connection we used the XT60.
The board model can be seen on Figure 4.

### 2.5 Assembly

In Figure 5 there is the assembly of all modules developed by the team. The radio and STM32 boards aren’t placed in the 3D model, but, their places and connectors are being considered. The radio board is the nRF24L01, which is the same from last years.
With these changes, we are looking for a structure that will simplify design developments for a new control board that will make it easier to make improvements, such as: achieve a better movement control with the new motor drivers,


Fig. 4. New main board.


Fig. 5. All modules assembled.

faster charging and higher durability of the kick board, making future improvements in electronics easier, since the structure is divided into several boards, in case of changes in one module the others will still work properly.

By analyzing previous (E)TDP from other teams [13,10,3], it is noticeable that a few years ago there was a majority of teams using FPGAs as the main controller of the robot. However, nowadays, there are a lot of teams using STM micro controllers instead.

Due to the great peripherals that the STM32 micro controller has, such as timers that can be configured to read the encoders, we’ve decided to migrate to it. That way, the development of a new firmware should be fairly easier than using a FPGA.

In a future version of our main board we plan to stop using the STM32F407 Discovery board and use only the STM32 chip, that way the board layout should be greatly simplified.

### 3 System Identification

In order to project a good controller it is important to have a good model of the plant which will be controlled. Therefore, some knowledge about the plant parameters is necessary, e.g. friction coefficients. However, some of the parameters can be hard to measure, thus, complicating the task of accurately modeling the plant using classical laws of physics. To avoid this problem there is a modeling technique called system identification, which consists of estimating/identifying the plant model using data from its input and output [6].

### 3.1 Plant excitation

As already said, to identify a certain model, it is necessary to have data from the input and output of the plant. Note that this data need to be as much informative about the plant behavior as possible. The identified model will only be able to reproduce behaviors that were captured by the data used in the estimation, thus, the importance of the data quality.
In order to gather informative data that result in a good model there are some commonly used signals which can be used. Those signals are: Pseudo Random Binary Signal (PRBS), Generalized Binary Noise (GBN) and Step function.

PRBS The PRBS signal is commonly used in system identification for linear systems, it is a deterministic signal with properties of a random signal [11]. Due to its white-noise like properties, this kind of signal is capable of exciting the dynamics of the plant in various frequencies. It can be generated using a Linear Feedback Shift Register (LFSR) [9], and is parameterized by the number of bits n in the shift register and the switching time Ts.

GBN The GBN is a stochastic binary signal which switches between two fixed levels [12]. At every time sample it has a probability p of switching to another level. This probability has to be correctly determined for each plant, [12] proposes some guidelines that can be used to choose a good value for p.

Step Signal Although it is considered as a poor signal, i.e. doesn’t provide much information about the system, it can be used when identifying simple systems. According to [12], it is better to use a step signal than a badly parameterized binary noise based signal. In the control area this is a widely used signal, most of the system parameters are acquired using the step response experiment [7].

### 3.2 Model formats

After choosing an input signal, it is necessary to pick a format for the model to be identified, there are several mathematical formats, the most common are: Transfer functions, Space State and Polynomials.

The model format is also an important choice to make, depending on the type of plant some models can adapt better than others. When dealing with linear Single Input Single Output (SISO) systems, a common choice is the transfer function [7].

### 3.3 Considerations About the Robot

Since the robots used in the SSL are omni-directional, its three axis are independent, thus, the whole robot can be considered as three separate SISO systems. By using the harmonic analysis method [5] it is possible to see that the X, Y and θ axis can be considered as linear, since, apart from the noise and some attenuation, there is no presence of other harmonics than the one present in the input, this can be seen on Figure 6, the signals used were Vi(t) = 0.75∗sin(t), i = x, y [SI] and Vθ(t) = 5.4 ∗ sin(t) [SI]. This analysis can also be verified by using the Discrete Fourier Transform, if the system is linear, the DFT of the input and output should be practically the same.


Fig. 6. Harmonic Analysis.

There is a considerable noise present in the data collected for the Y and θ axis presented in Figure 6. This happens because these velocities were calculated based on the raw position of the robot.
Figure 6 also shows a small phase shift for the X axis, a possible cause for this is the influence of the angle that the robot is facing (θ). During the tests it was noticed that depending on the value of θ, when working in a open loop, there may be a slight phase shift and even some attenuation for the X axis. This effect doesn’t seem to be noticeable in the Y axis.

### 4 Identifying the Models

To actually do the identification of the models, the System Identification Toolbox from MATLAB was used. The toolbox interface can be seen on Figure 7. The first step is to import the working data. After importing the data, in the ’Estimate →’ option it is possible to choose which model it will estimate, e.g. transfer function model, and then the model output can be seen by clicking on the ’Model output’ checkbox.


Fig. 7. System Identification Toolbox interface.

Being a linear SISO system facilitates a lot of the process of identifying the models of our robots, as well as the controller project. Therefore, the model format of choice was the transfer function, due to the ease of applying classical control theory on it.
Given that the purpose of the model is to design a position controller for our robots, the model input will be the velocities Vx, Vy, and Vθ, which are the velocities that the robot must move in the X, Y and θ axis in the field reference. The model output will be the field position of the robot in each axis.

### 4.1 Data Acquisition

As said earlier, the quality of the working data is crucial for a good model estimation. One thing that needs to be assured when gathering the data is the sampling interval, since the models will likely be used in its discrete form, the sampling interval must be constant. Given that the actual control loop runs at a 15ms interval, it will be the sampling time used.
To guarantee that the signals will be sent and measured in the right interval, a dedicated software was built. Basically it is responsible for generating any of the signals commonly used in the process of identification, i.e. PRBS, GBN, Step and Sine, sending these signals to the robots and measuring the position of the robot. In Figure 8 it is possible to see the software interface, at the bottom left there are some graphs to see the signal being sent, in the top right there are the parameters of each type of signal. In the future, the software will be integrated with MATLAB to make it easier to generate the models.


Fig. 8. System Identification Software.

### 4.2 Input Signal

Since the model format is a transfer function, the step response experiment was used to collect the data needed. Some previous experiments have shown that it is possible to estimate good models using this experiment.
The measured data can be seen of Figures 9 and 10. Note that this is an open loop experiment, therefore, it is expected that the X,Y and θ values tend towards infinity.

### 4.3 Models

When using the tools that MATLAB offers to identify transfer function models it is necessary to set how many poles and zeros the transfer function must have. By doing some experiments it was discovered that the robot behavior can be


Fig. 9. X and Y Input Data.


Fig. 10. θ Input Data.

accurately modeled using two poles and none zeros, and in some cases two poles and one zero.
Using the data shown in Section 4.2 the discrete transfer functions for the X, Y and θ axis were identified and can be seen on Equations (1), (2) and (3).

Px(z)
Vx(z)

=

0.0003494
z

2 − 1.97z + 0.97

(1)

Py(z)
Vy(z)

=

0.0006378
z

2 − 1.94z + 0.9399

(2)

Pθ(z)
Vθ(z)

=

0.001623
z

2 − 1.901z + 0.9009

(3)

The compare command outputs a graph which show how close the model output is to the given data. On Figures 11 and 12 it is possible to see that all models have more than 97% of accuracy when representing the robot.


Fig. 11. X and Y Model Output.


Fig. 12. θ Model Output.

These results show that the models can accurately represent the behavior of the robot, therefore, it is now possible to design the position controller.

### 5 Position Controller

By having the models of the robot, it is possible to design the position controller that gets the robots to its destiny.

The controller of choice is the classic Proportional Integrative Derivative (PID)[7]. It is a very robust controller and can be easily tuned using MATLAB and its PID Tuner Toolbox.

### 5.1 Tunning the Controller

The first step to tune the controllers is to create the block diagrams in Simulink, the result for the X axis can be seen on Figure 13. For Y and θ axis it is exactly the same diagram, except for the transfer function model values.


Fig. 13. Block diagram to tune the X axis controller.

The windup effect is caused by an overflow of the integrator in the loop. It usually happens when the plant saturates for an extended period of time and the integrator continues to integrate the error [4]. Therefore, it is important to have some kind of anti-windup method.
The PID block offers two anti-windup methods. The one chosen for this application is the clamping method. It is one type of conditional integration and works by stopping the integrator once the system meets a certain condition [2,1]. The saturation limits must also be defined, the values chosen were ±1.75 m/s, which is the highest speed the robots can drive without too much slipping. For the angular velocity the limits are ±6.25 rad/s.
Using the ’Tune’ button in the PID block it is possible to tune the controller. The PID Tuner interface can be seen on Figure 14. In this example, the tuned system performance parameters can be seen on Table 1.

Table 1. System performance parameters.

| Rise time [s] | Settling time [s] | Overshoot [%]
X | 1.05 | 3.48 | 9.8
Y | 0.795 | 2.19 | 3.84
θ | 0.165 | 0.525 | 7.03

Using the two sliders on the top of the window (Tuning Tools upper section) it is possible to adjust the transient response of the system, the effects of the


Fig. 14. PID Tuner example for the X axis.

changes can be seen on the step plot. The design focus can be changed to ’Reference tracking’ (Controller upper section). This option helps to diminish the overshoot.
During a few experiments, the controllers that behaved better on the actual robots were the ones that had a smooth control effort, therefore, adding its plot is helpful (Design upper section) in the tuning process.
The controller block can be updated using the ’Update Block’ button.

### 5.2 Deploying the Controller

After tuning the controllers for all axes it is time to implement them in the strategy software. By doing a few adjustments to the block diagram in Simulink it is possible to export it to C++ code using the Embedded Coder feature. The final block diagram can be seen on Figure 15.


Fig. 15. Block diagram to export the X axis controller to C++.

Basically, all that needs to be done is to add the inputs/outputs blocks to the control loop, e.g. set-point position, feedback, output to the system. This step is important because this is how MATLAB will know what variables must be added to interact with the generated code.

### 5.3 Results

The new controller showed some reasonably good results and the improvements in the speed and precision of the robot are visibly noticeable. The step response for all axes can be seen on Figure 16.


Fig. 16. Step response for all axes of the robot.

The measured system parameters can be seen on Table 2.

Table 2. Measured system performance parameters.

| Rise time [s] | Settling time [s] | Overshoot [%]
X | 1.785 | 3.299 | 0
Y | 1.275 | 3.210 | 0
θ | 0.150 | 0.735 | 9.287

Note that for the θ axis, the variation on the system parameters is smaller than for the X and Y axes. During θ test there wasn’t as much slipping as there was for the other two, which clearly resulted in it being closer to the theoretical parameters.
At the beginning of the X and Y tests there as a slight slipping of the wheels, which most likely resulted in its parameters having a higher deviation from the theoretical ones. Slipping is an example on non-linearity that may happen in the system. However, it can be fixed by doing a few improvements in the control loop of the wheels itself, e.g. a better handling of its acceleration, which is currently absent.

### 6 Acknowledgements

We would like to thank, in advance, the Small Size League Committee, for the consideration of our material. We would like also to immensely thank the staff of Centro Universit´ario FEI, for all the help we always received from them.

References

1. ˚Astr¨om, K.J., H¨agglund, T., Astrom, K.J.: Advanced PID control, vol. 461. ISA-The Instrumentation, Systems, and Automation Society Research Triangle. (2006)
2. Bohn, C., Atherton, D.: An analysis package comparing pid anti-windup strategies. IEEE Control Systems Magazine 15(2), 34–40 (1995)
3. Chen, L., Jin, L., Lon, C.W., Wen, L., Gu, J., Li, J., Fang, T., Xiong, R.: Zjunlict extended team description paper for robocup 2018. RoboCup Wiki as extended team description of ZJUNlict, Montreal, Canada, accessed March 6, 2019 (2018)
4. Guzm´an, J.L., ˚Astr¨om, K.J., Dormido, S., H¨agglund, T., Piguet, Y.: Interactive learning modules for pid control. IFAC Proceedings Volumes 39(6), 7–12 (2006)
5. Hosseini, S.M., Johansen, T.A., Fatehi, A.: Comparison of nonlinearity measures based on time series analysis for nonlinearity detection (2011)
6. Ljung, L.: System identification. In: Signal analysis and prediction, pp. 163–173. Springer (1998)
7. Ogata, K., Yang, Y.: Modern control engineering, vol. 4. Prentice hall India (2002)
8. de Oliveira, G.P., Alves, V.M., Pilotto, D., de S. Motta, W., da S. Costa, L., Pauli, G.L., et al.: Robofei 2019 team description paper. . (2019)
9. Panda, A.K., Rajput, P., Shukla, B.: Fpga implementation of 8, 16 and 32 bit lfsr with maximum length feedback polynomial using vhdl. In: 2012 International Conference on Communication Systems and Network Technologies. pp. 769–773. IEEE (2012)
10. Ryll, A., Ommer, N., Geiger, M., Jauer, M., Theis, J.: Tigers mannheim
11. Tangirala, A.K.: Principles of system identification: theory and practice. Crc Press (2014)
12. Tulleken, H.J.: Generalized binary noise test-signal concept for improved identification-experiment design. Automatica 26(1), 37–49 (1990)
13. Vedder, K., Schneeweiss, E., Rabiee, S., Nashed, S., Lane, S., Holtz, J., Biswas, J., Balaban, D.: Umass minutebots 2017 team description paper (2017)

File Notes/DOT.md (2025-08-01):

[[Robot Soccer]]
# Attendus :

### Objectif : présenté le déroulé chronologique du projet 

Ce déroulé opérationnel permet de mettre en valeur de façon synthétique les Étapes ou Séquences clés du TIPE. Il apporte aux examinateurs des éléments chronologiques sur l’exécution du TIPE, et qui ne sont pas nécessairement à mentionner dans la présentation orale. Il serait utile que certains éléments de ce DOT soient mis en rapport avec les objectifs annoncés dans la MCOT.

Ce DOT est une séquence de 4 à 8 faits marquants (jalons) du déroulement du TIPE (y compris les difficultés rencontrées, surmontées ou non) témoignant de sa progression. Chacune de ces Étapes ou Séquences clés y est décrite dans la limite de 50 mots et saisie en ligne via l’interface SCEI.

Le DOT **ne doit pas être analogue à un plan, ni fournir des résultats ou des interprétations**. Il doit, avant tout, rester factuel et situer chronologiquement les différents jalons.

Le DOT peut être aussi l'occasion d'indiquer les éventuelles difficultés rencontrées, la manière dont elles ont été surmontées ou non, les rebonds ou inflexions dans la démarche, soulignant ainsi la progression effective du travail, permettant aux examinateurs d'avoir une meilleure lisibilité du "cheminement" du candidat.

Exemples de formulation d’Étapes ou Séquences clés : 

- Début Mars : Rencontre avec un expert en vibration des machines tournantes. Cette discussion m’a amené à lire les références [n] et [m], permettant l’identification des paramètres clés de l’étude 

- Novembre 2023 - Identification de notre méthode comme étant la théorie de De Bruijn, pour laquelle des algorithmes de résolution existent et sont disponibles en libre accès 

- Décision fin mai - Suite à la lecture de l’article [2] - d’étudier la sensibilité de manière théorique via le conditionnement des matrices. Cela s’est avéré infructueux puisque les différents facteurs que nous avions isolés n’étaient pas indépendants 

- Février 2024 - Réalisation d’une série d’expériences en faisant varier les deux paramètres a et b, ce qui nous a amenés à conjecturer la loi empirique. Le résultat est satisfaisant, mais dans un domaine de validité réduit]

- Mi-janvier 2024- Compréhension du lemme de Proob 

- Fin décembre : Passage de la version récursive à la version itérative de l’algorithme, au prix d’une augmentation peu significative du temps de calcul 

- Janvier 2024 - Échec de la synthèse d’un organomagnésien après les premières tentatives du début d’année nous obligeant à revoir les conditions de l’expérience 

- Mai 2024 : Réussite de la nouvelle synthèse de l’organomagnésien et calcul du rendement

- Début Juin 2024- Interprétation des résultats, estimation des incertitudes de mesure, production des courbes pertinentes pour la présentation finale]

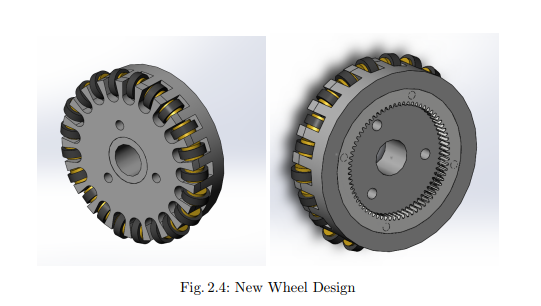
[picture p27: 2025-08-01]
Images illustrations/2020 Team Description Paper UBC Thunderbots.png

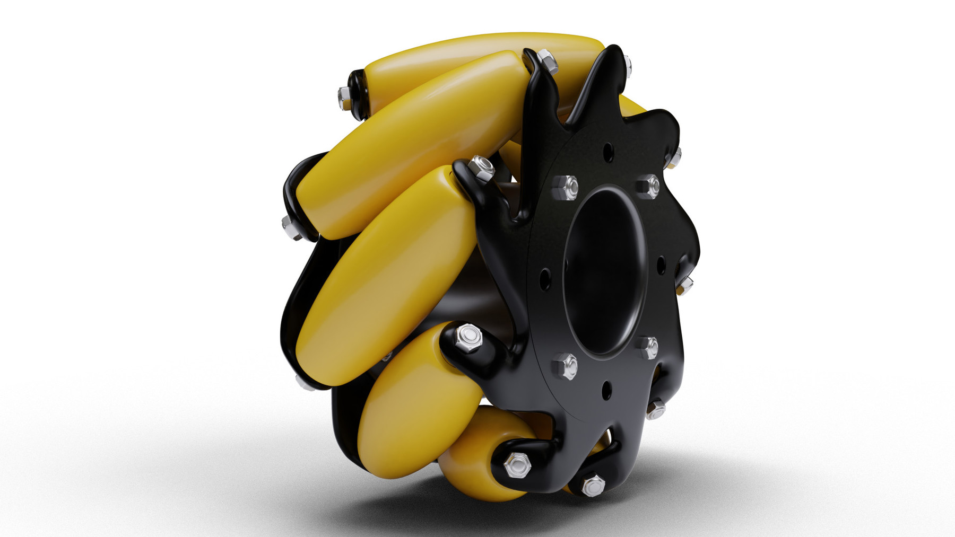
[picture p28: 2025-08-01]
Images illustrations/file-1428963736.jpg

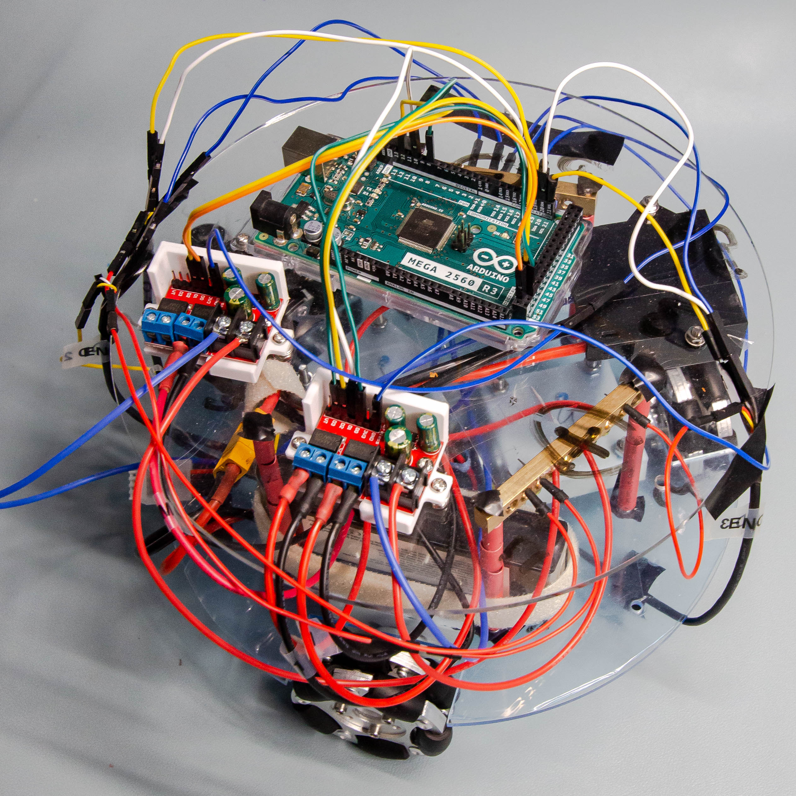
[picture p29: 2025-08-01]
Images illustrations/06062024-_MG_3204.jpg

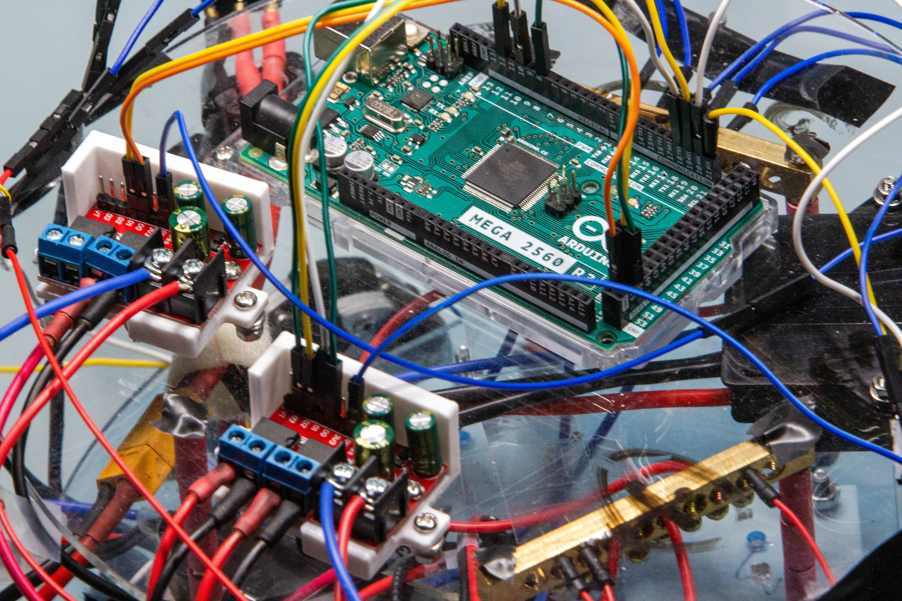
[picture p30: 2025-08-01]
Images illustrations/05062024-_MG_3197.jpg

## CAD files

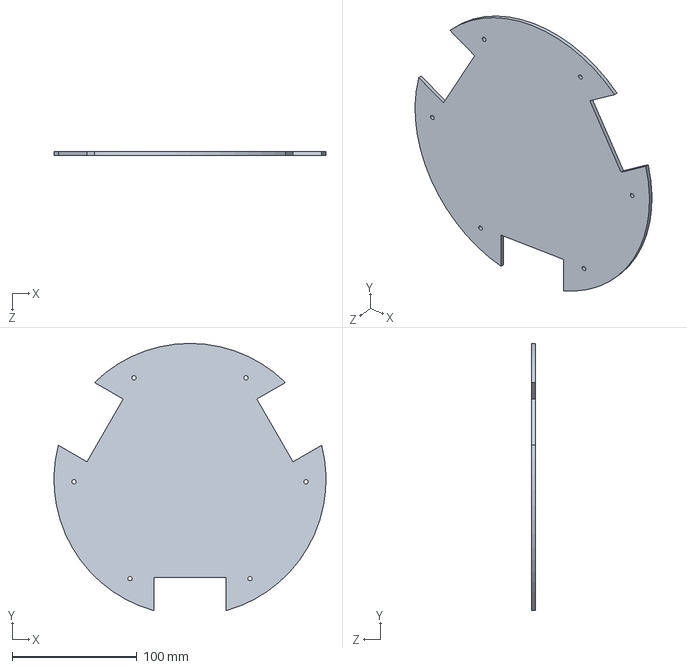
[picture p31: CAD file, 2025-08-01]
Réalisation/3D/Modèle extérieur/Chassis moteur Assemblage.SLDPRT
217.9 x 214.1 x 3.00 mm

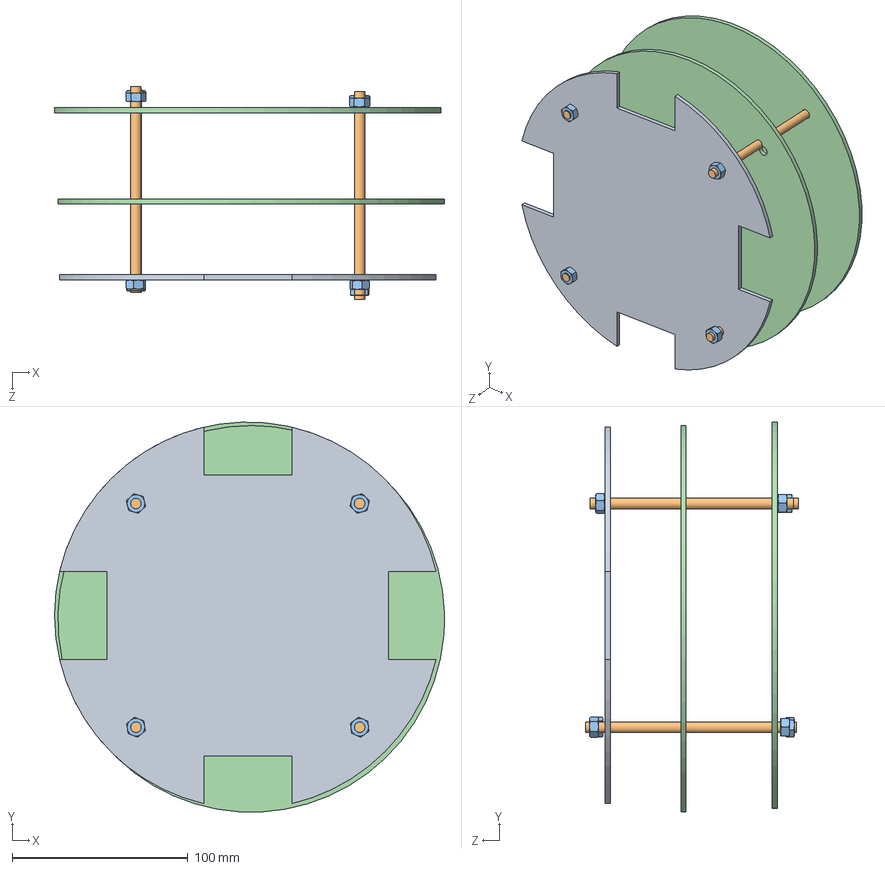
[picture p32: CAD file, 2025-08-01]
Réalisation/3D/assemblage structure de base 1er jet.SLDASM
221.9 x 221.8 x 121.0 mm
chassis
espaceur x 4
ECROU H x 8
chassis superieur x 2

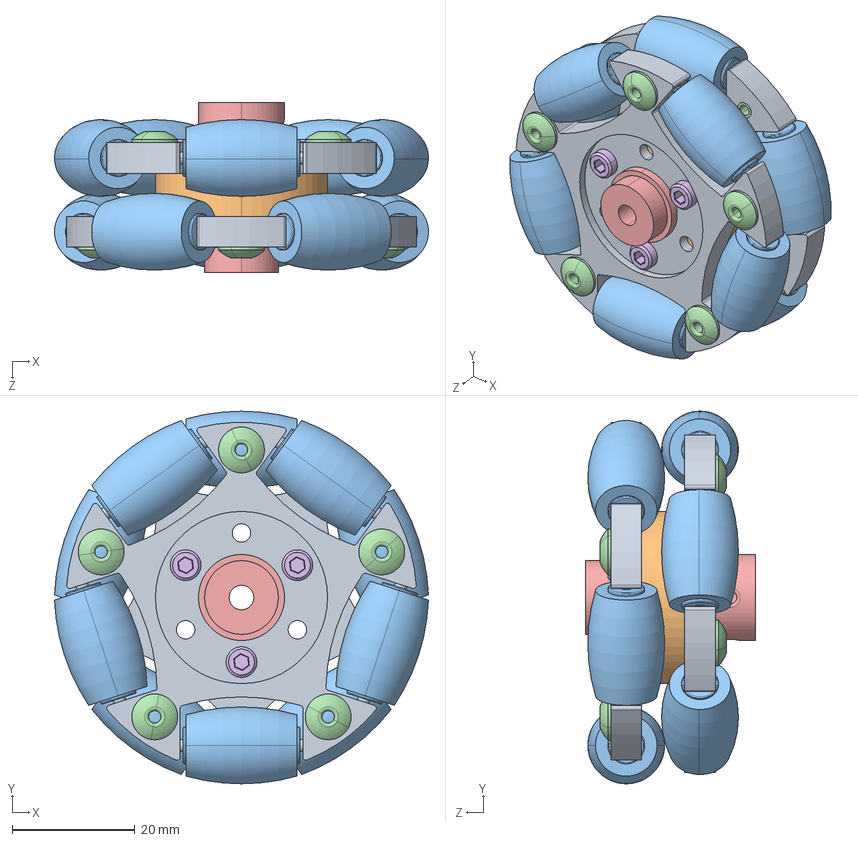
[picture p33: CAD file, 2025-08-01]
Réalisation/3D/Modèle extérieur/WheelAsm.STEP
60.8 x 60.6 x 27.6 mm
WheelBase x 2
BasePlacer
RubberWheel x 10
Rivet x 10
ShaftConnector
M3HexNut x 6

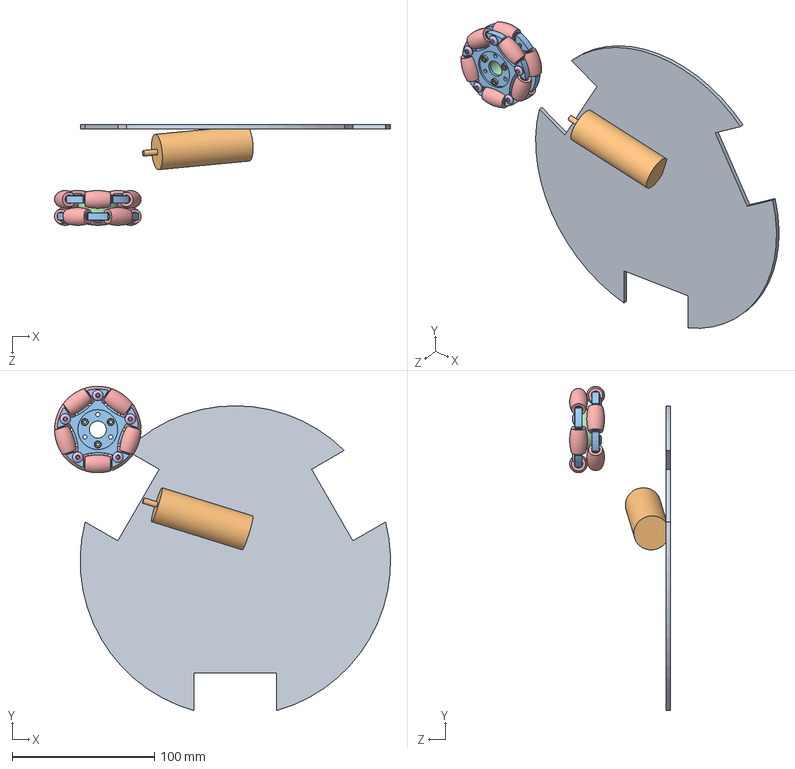
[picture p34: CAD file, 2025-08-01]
Réalisation/3D/Modèle extérieur/Assemblage1.SLDASM
236.0 x 227.7 x 70.7 mm
Chassis moteur
Moteur
WheelBase x 2
BasePlacer
RubberWheel x 10
Rivet x 10
M3HexNut x 6

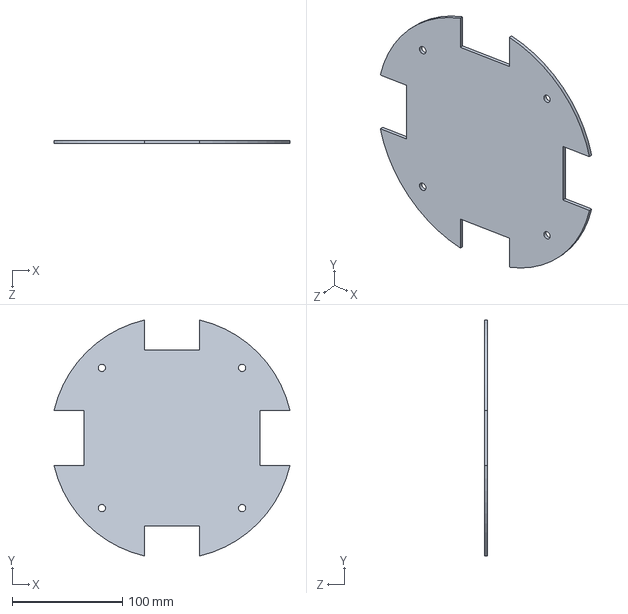
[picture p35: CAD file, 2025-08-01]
Réalisation/3D/Chassis/chassis.SLDPRT
214.2 x 214.2 x 3.00 mm

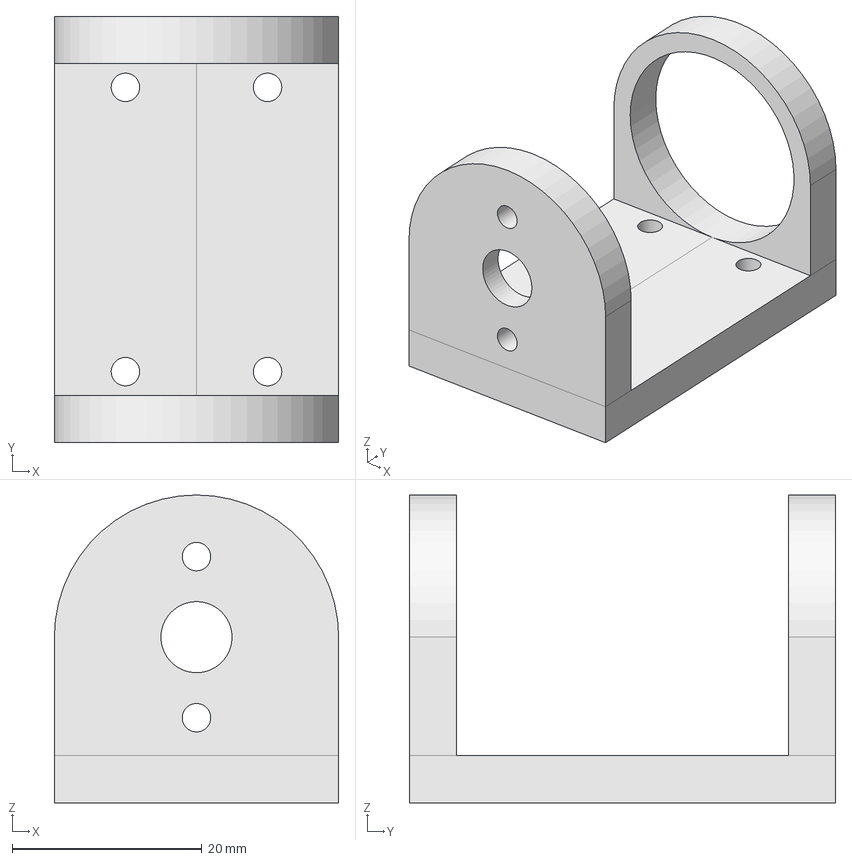
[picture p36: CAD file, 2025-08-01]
Réalisation/3D/Modèle extérieur/files/Dagu-motor-mounting.fcstd
30.0 x 45.0 x 32.5 mm

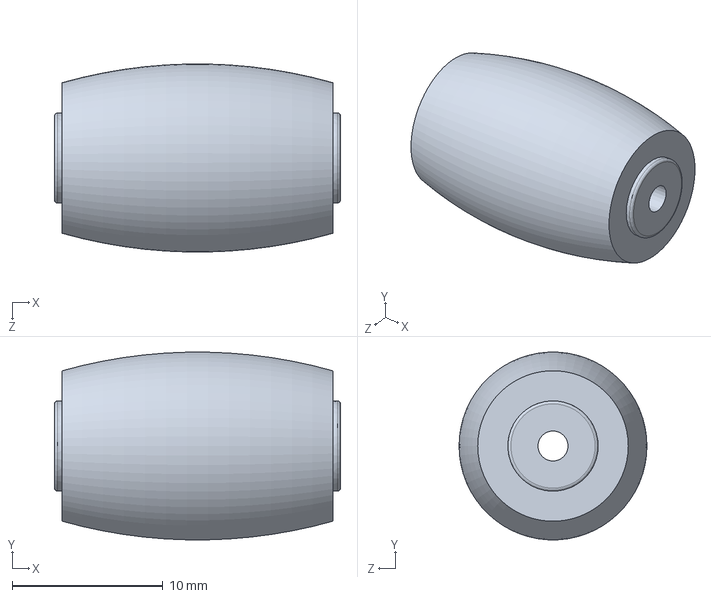
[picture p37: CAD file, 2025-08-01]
Réalisation/3D/Modèle extérieur/Omni/RubberWheel.SLDPRT
19.0 x 12.5 x 12.5 mm

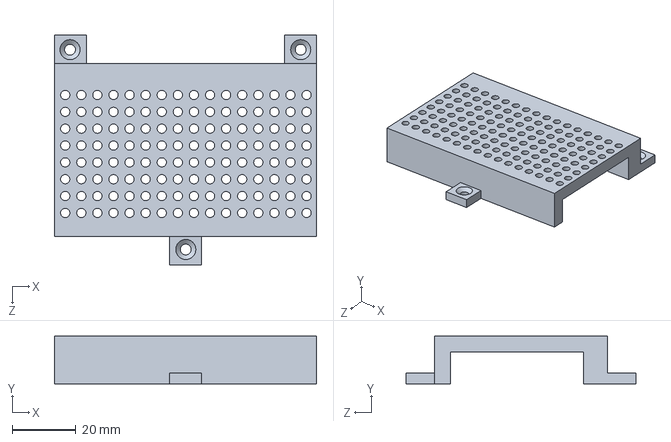
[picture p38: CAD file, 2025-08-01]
Réalisation/3D/Support breadbord.SLDPRT
82.0 x 15.0 x 72.0 mm

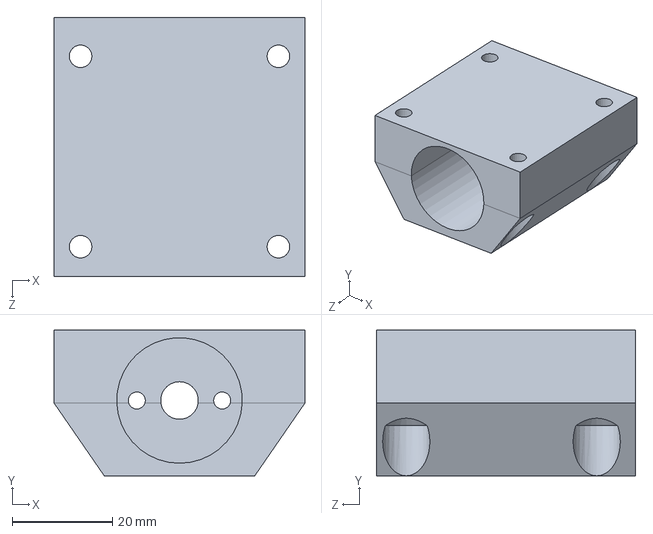
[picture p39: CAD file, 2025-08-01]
Réalisation/3D/Support moteur/Corrompus/Support Moteur.SLDPRT
50.0 x 29.0 x 51.5 mm

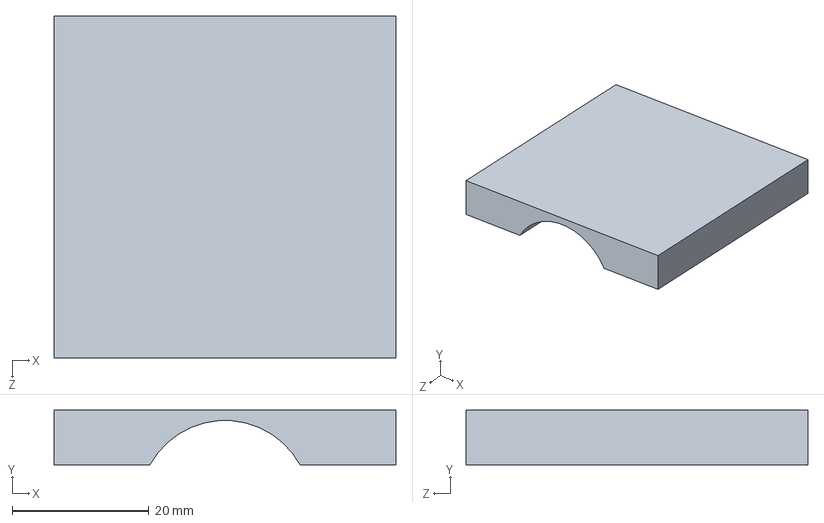
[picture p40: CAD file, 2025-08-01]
Réalisation/3D/Support moteur/PArtie Basse V2.SLDPRT
50.0 x 8.00 x 50.0 mm

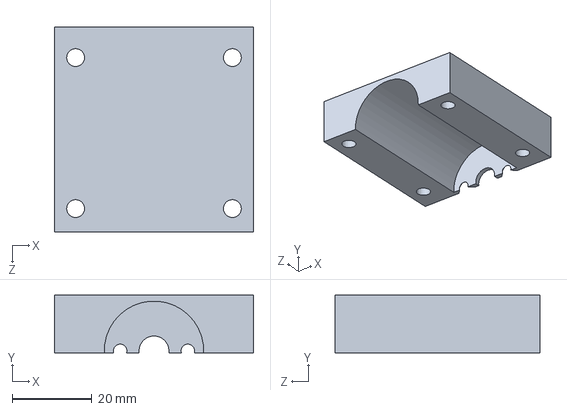
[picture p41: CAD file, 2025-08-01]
Réalisation/3D/Support moteur/V3/Partie Basse.SLDPRT
50.0 x 14.5 x 51.5 mm

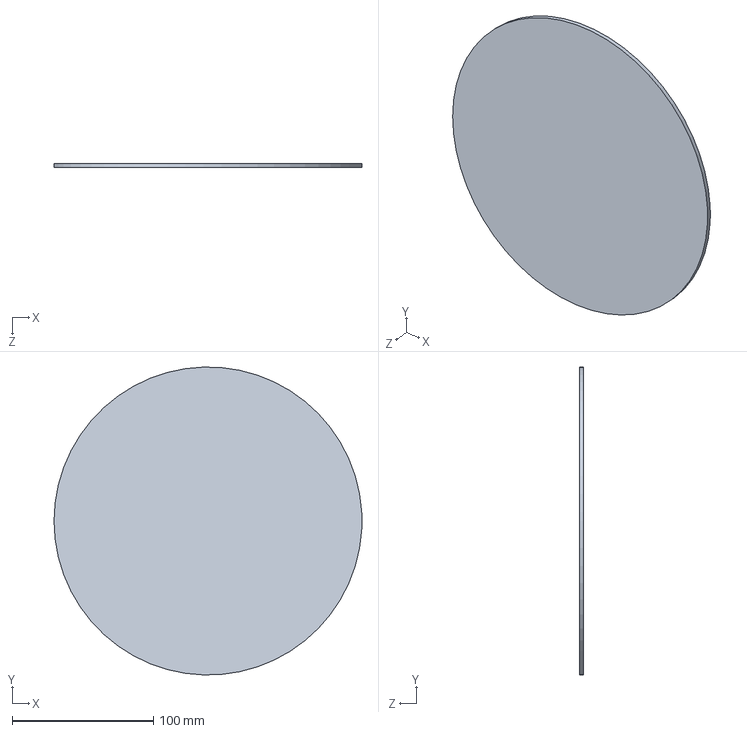
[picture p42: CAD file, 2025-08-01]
Réalisation/3D/Chassis/chassis superieur.SLDPRT
218.0 x 217.9 x 3.00 mm

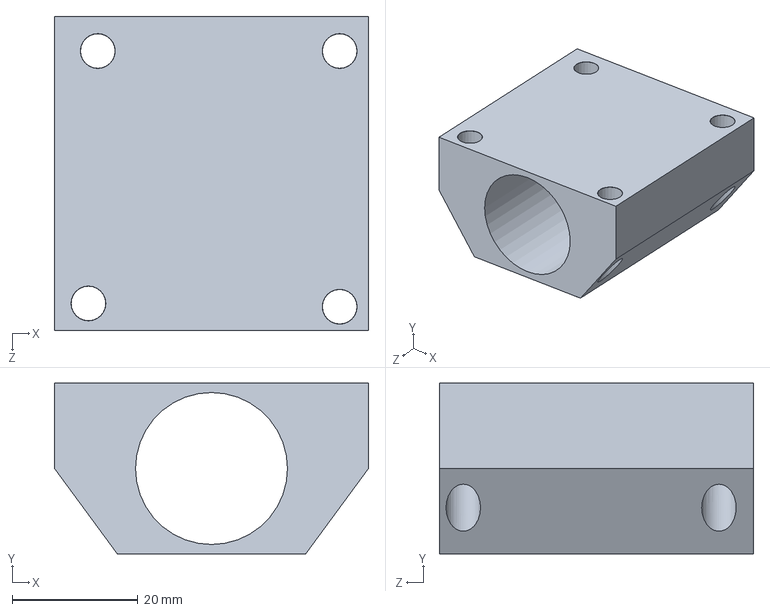
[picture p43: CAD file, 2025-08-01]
Réalisation/3D/Corps1.SLDPRT
50.0 x 27.2 x 50.0 mm

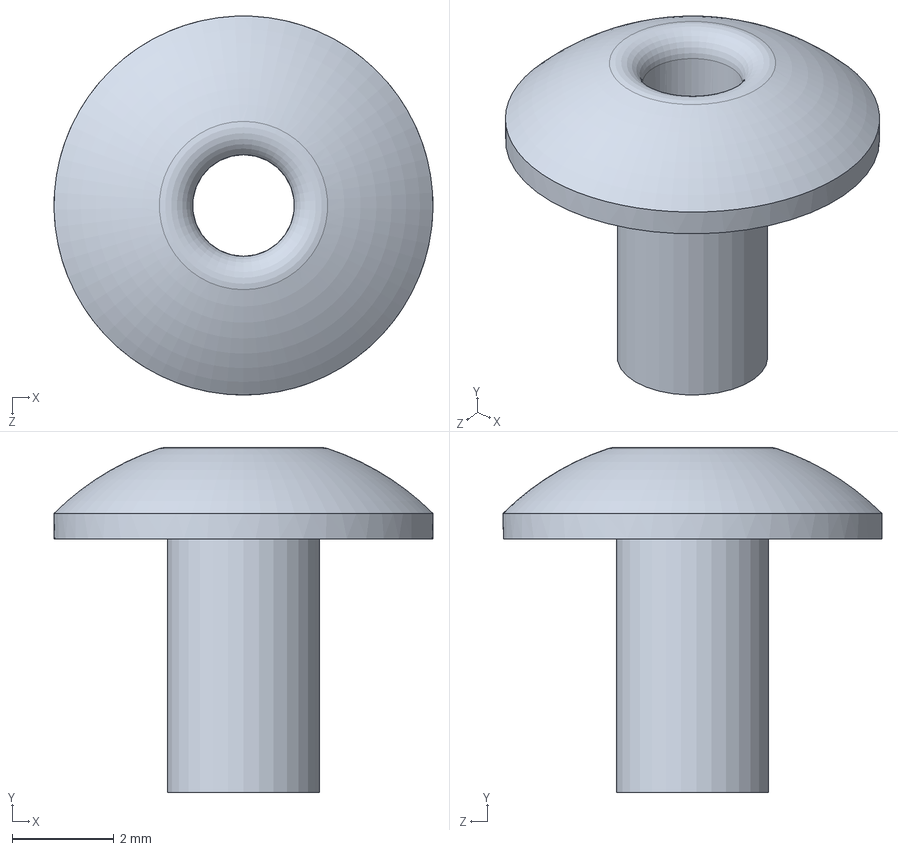
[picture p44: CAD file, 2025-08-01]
Réalisation/3D/Modèle extérieur/Omni/Rivet.SLDPRT
7.46 x 6.80 x 7.46 mm

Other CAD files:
Réalisation/3D/Modèle extérieur/Chassis moteur.SLDPRT.SLDASM
Réalisation/3D/Modèle extérieur/Omni/WheelAsm.SLDASM
Réalisation/3D/Modèle extérieur/Chassis moteur.SLDPRT
Réalisation/3D/Support moteur/Corrompus/Partie Haute V3.SLDPRT
Réalisation/3D/Modèle extérieur/Moteur.SLDPRT
Réalisation/3D/Modèle extérieur/Omni/BasePlacer.SLDPRT
Réalisation/3D/Modèle extérieur/Omni/M3HexNut.SLDPRT
Réalisation/3D/Modèle extérieur/Omni/ShaftConnector.SLDPRT
Réalisation/3D/Modèle extérieur/Omni/WheelBase.SLDPRT
Réalisation/3D/Modèle extérieur/WheelAsm.SLDASM
Réalisation/3D/Modèle extérieur/files/Dagu-motor-mounting.stl
Réalisation/3D/Support breadbord.STL
Réalisation/3D/Support driver abaisseur.SLDPRT
Réalisation/3D/Support driver abaisseur.STL
Réalisation/3D/Support driverSLDPRT.SLDPRT
Réalisation/3D/Support driverSLDPRT.STL
Réalisation/3D/Support moteur/Corrompus/Partie Basse V3.SLDPRT
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

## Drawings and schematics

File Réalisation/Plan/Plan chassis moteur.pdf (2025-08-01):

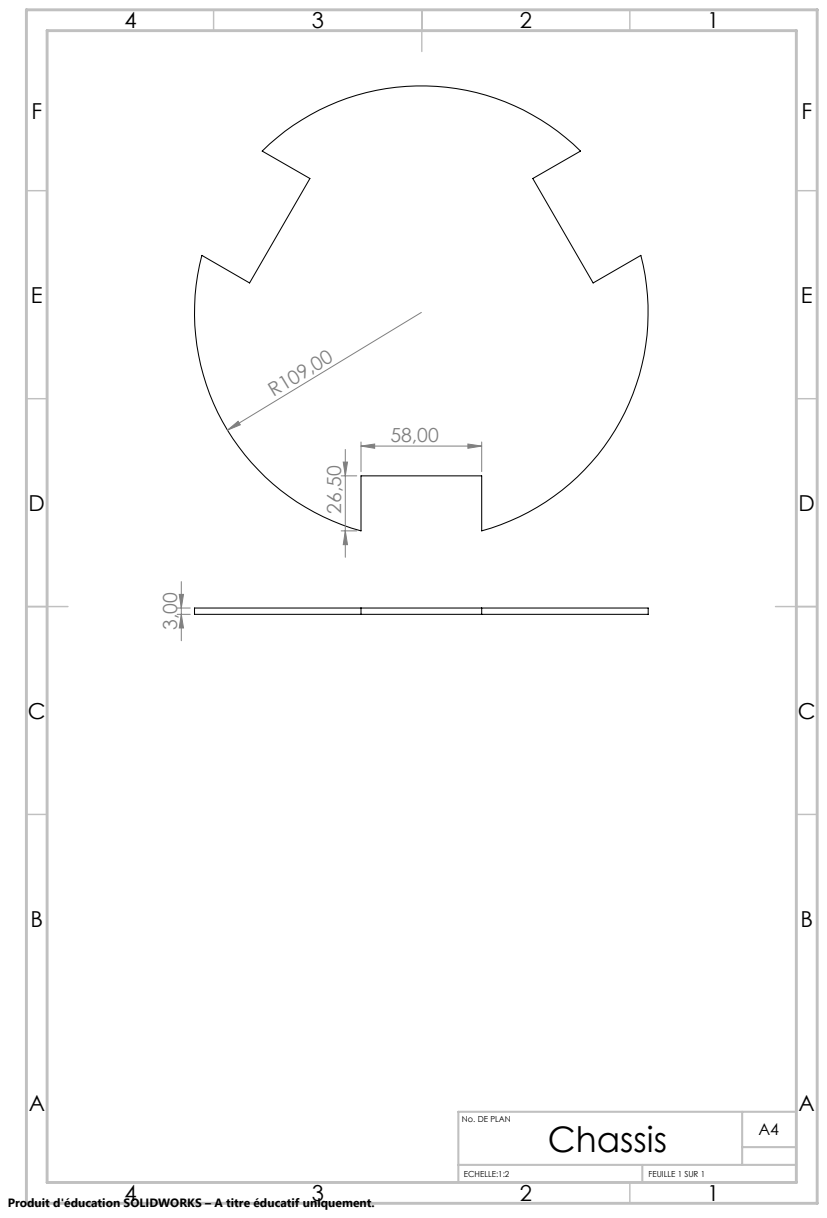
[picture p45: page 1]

No. DE PLAN | A4 Chassis

ECHELLE:1:2 | FEUILLE 1 SUR 1

Produit d'éducation SOLIDWORKS – A titre éducatif uniquement.

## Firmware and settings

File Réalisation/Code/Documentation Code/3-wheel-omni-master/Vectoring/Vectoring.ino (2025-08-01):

/*  AETR
     RC override
    On the serial monitor write : 111,111*111 where  <magnitude,angle*rotation>
*/

//encoder initializations
#define encoder1PinA  2    //motor 1
#define encoder1PinB  3
long unsigned int encoder1Pos = 1000;
#define encoder2PinA  18    //motor 2
#define encoder2PinB  19
long unsigned int encoder2Pos = 1000;
#define encoder3PinA  20    //motor 3
#define encoder3PinB  21
long unsigned int encoder3Pos = 1000;

volatile int cps1 = 0;
volatile int cps2 = 0;
volatile int cps3 = 0;

//motor intializations
const int inAPin1 = A5;
const int inBPin1 = A4;
const int PWMPin1 = 8;

const int inAPin2 = A2;
const int inBPin2 = A3;
const int PWMPin2 = 9;

const int inAPin3 = A0;
const int inBPin3 = A1;
const int PWMPin3 = 10;

int i = 0;                            //used by timing ISR

int pwm1 = 0;
int cps1_des = 0;
double output1 = 0;

int pwm2 = 0;
int cps2_des = 0;
double output2 = 0;

int pwm3 = 0;
int cps3_des = 0;
double output3 = 0;

int temp1 = 1000;
int temp3 = 1000;
int temp2 = 1000;

//**************************************
//*********SETUP FUNCTION***************
//**************************************
void setup() {
  // motor setup
  pinMode(inAPin1, OUTPUT);
  pinMode(inBPin1, OUTPUT);
  pinMode(PWMPin1, OUTPUT);

  pinMode(inAPin2, OUTPUT);
  pinMode(inBPin2, OUTPUT);
  pinMode(PWMPin2, OUTPUT);

  pinMode(inAPin3, OUTPUT);
  pinMode(inBPin3, OUTPUT);
  pinMode(PWMPin3, OUTPUT);


  //encoder setup, 
  pinMode(encoder1PinA, INPUT); //Rend les encoder opérationnels
  digitalWrite(encoder1PinA, HIGH);
  pinMode(encoder1PinB, INPUT);
  digitalWrite(encoder1PinB, HIGH);
  attachInterrupt(digitalPinToInterrupt(2), doEncoder1, CHANGE);  // encoder pin on interrupt 2
  //Lorque que l'necoder detecte un changement il declenche doEncoder1, qui fais quelque chose sur encoder1Pos

  pinMode(encoder2PinA, INPUT);
  digitalWrite(encoder2PinA, HIGH);
  pinMode(encoder2PinB, INPUT);
  digitalWrite(encoder2PinB, HIGH);
  attachInterrupt(digitalPinToInterrupt(18), doEncoder2, CHANGE);  // encoder pin on interrupt 18

  pinMode(encoder3PinA, INPUT);
  digitalWrite(encoder3PinA, HIGH);
  pinMode(encoder3PinB, INPUT);
  digitalWrite(encoder3PinB, HIGH);
  attachInterrupt(digitalPinToInterrupt(20), doEncoder3, CHANGE);  // encoder pin on interrupt 20


  //Serial setup
  Serial.begin (115200);


  // TIMER 1 for interrupt frequency 5 Hz:
  // Les timer devrait servire pour gerer les PWM
  cli(); // stop interrupts
  TCCR1A = 0; // set entire TCCR1A register to 0
  TCCR1B = 0; // same for TCCR1B
  // Initilisation du Timer1 pour les deux registres de controle A et B, les deux registres sont sur 8bit pour
  // avoir 16bit au final,  

  TCNT1  = 0; // initialize counter value to 0
  // set compare match register for 5 Hz increments
  // 
  // Le compteur est incrementer ou decrementer d'une unité a chaque top d'horloge 
  OCR1A = 49999; // = 16000000 / (64 * 5) - 1 (must be <65536)
  // turn on CTC mode
  TCCR1B |= (1 << WGM12);
  // Set CS12, CS11 and CS10 bits for 64 prescaler
  TCCR1B |= (0 << CS12) | (1 << CS11) | (1 << CS10);
  // enable timer compare interrupt
  TIMSK1 |= (1 << OCIE1A);
  sei(); // allow interrupts

  //RC override
  pinMode(4, INPUT);
  pinMode(6, INPUT);
  pinMode(7, INPUT);
  pinMode(8, INPUT);
  pinMode(9, INPUT);
  pinMode(10, INPUT);
  pinMode(13, OUTPUT);
  pinMode(30, INPUT);

}
//**************END OF SETUP FUNCTION****************************

int err_new1 = 0;
int err_old1 = 0;
int err_d11 = 0;
int err_d21 = 0;

int err_new2 = 0;
int err_old2 = 0;
int err_d12 = 0;
int err_d22 = 0;

int err_new3 = 0;
int err_old3 = 0;
int err_d13 = 0;
int err_d23 = 0;

int v1;
int v2;
int v3;
float vel_x;
float vel_y;
float theta;
int magnitude;

// for PID
float adj = 1;
float Kp = 0.3;

int d1;                           // for direction of rotation of motors
int d2;
int d3;

//for serial comm
char buf[12];
String mov;


//RC override
int flag = 0;
int a;
int e;
int t;
float Speed = 0;
float Theta = 0;
float Rot = 0;

void loop()
{
  char rxBuf[12];
  if (digitalRead(30) == 0)
  {
    if (Serial.available() >= 4)         //Each data packet is 7 characters, 3 - throttle, 3 - steering
    {
      char readChar = Serial.read();
      if (readChar == 'A')
      {
        while (Serial.available() < 12);    //Wait for 12 characters to be read
        for (int i = 0; i < 12; i++)        // Read 6 characters iteratively
          rxBuf[i] = Serial.read();
        //for (int j = 0; j < 12; j++)        // Loop to display the array read
        //Serial.print(rxBuf[j]);
        //Serial.println("*****");

        Speed = 100 * ((float)rxBuf[1] - 48) + 10 * ((float)rxBuf[2] - 48) + 1 * ((float)rxBuf[3] - 48);
        Theta = 100 * ((float)rxBuf[5] - 48) + 10 * ((float)rxBuf[6] - 48) + 1 * ((float)rxBuf[7] - 48);
        Rot = 100 * ((float)rxBuf[9] - 48) + 10 * ((float)rxBuf[10] - 48) + 1 * ((float)rxBuf[11] - 48);
        //Serial.println(Speed);
        //Serial.println(Theta);
        //Serial.println(Rot);
        if (rxBuf[8] == 45)
        { flag = 1;
        }
        else flag = 0;
      }
    }
    if (flag == 1)
      base11(Speed, Theta, Rot);
    else if (flag == 0)
      base1(Speed, Theta, Rot);
  }
  else if (digitalRead(30) == 1)
  {
    digitalWrite(13, HIGH);
    a = pulseIn(7, HIGH);    //channel 1 (A)
    e = pulseIn(6, HIGH);    //channel 2 (E)
    t = pulseIn(4, HIGH);    //channel 3 (T)
    base2(a, e, t);
  }
}


//=============== Serial read=============
int readline(int readch, char *buffer, int len)
{
  static int pos = 0;
  int rpos;
  if (readch > 0)
  {
    switch (readch)
    {
      case '\r': //ignore carriage return
        break;
      case '\n': // return on new line
        rpos = pos;
        pos = 0;
        return rpos;
      default:
        if (pos < len - 1)
        {
          buffer[pos++] = readch;
          buffer[pos] = 0;
        }
    }
  }
  return 0;
}

//===================Serial parse and Base command  ========================
void parseCommand(String com)
{
  String part1;
  String part2;
  String part3;
  part1 = com.substring(0, com.indexOf(','));                           // vector magnitude
  part2 = com.substring(com.indexOf(',') + 1, com.indexOf(',') + 4 );   // vector angle
  part3 = com.substring(com.indexOf('*') + 1, com.indexOf('*') + 4);    // rotation speed
  int mag = part1.toInt();
  mag = abs(mag);
  int ang = part2.toInt();
  ang = abs(ang);
  int rot = part3.toInt();
  base1(mag, ang, rot);
}


//============================== Vectoring via serial =======================
void base1(float magnitude, float theta, int rot )
{
  theta = theta * 0.0174533;              //convert from deg angle to radian
  vel_x = magnitude * cos(theta);
  vel_y = magnitude * sin(theta);

  const float sqrt3o2 = 1.0 * sqrt(3) / 2;
  float v1 = - vel_x + rot;
  float v2 = 0.5 * vel_x - sqrt3o2 * vel_y + rot;
  float v3 = 0.5 * vel_x + sqrt3o2 * vel_y + rot;

  d1 = 0;
  d2 = 0;
  d3 = 0;
  d1 = v1 < 0 ? -1 : 1;
  d2 = v2 < 0 ? -1 : 1;
  d3 = v3 < 0 ? -1 : 1;

  v1 = map(abs(v1), 0, 100, 0, 550);
  v2 = map(abs(v2), 0, 100, 0, 550);
  v3 = map(abs(v3), 0, 100, 0, 550);

  M1(v1, d1);
  M2(v2, d2);
  M3(v3, d3);
}

void base11(float magnitude, float theta, int rot )
{
  theta = theta * 0.0174533;              //convert from deg angle to radian
  vel_x = magnitude * cos(theta);
  vel_y = magnitude * sin(theta);

  const float sqrt3o2 = 1.0 * sqrt(3) / 2;
  float v1 = - vel_x - rot;
  float v2 = 0.5 * vel_x - sqrt3o2 * vel_y - rot;
  float v3 = 0.5 * vel_x + sqrt3o2 * vel_y - rot;

  d1 = 0;
  d2 = 0;
  d3 = 0;
  d1 = v1 < 0 ? -1 : 1;
  d2 = v2 < 0 ? -1 : 1;
  d3 = v3 < 0 ? -1 : 1;

  v1 = map(abs(v1), 0, 100, 0, 550);
  v2 = map(abs(v2), 0, 100, 0, 550);
  v3 = map(abs(v3), 0, 100, 0, 550);

  M1(v1, d1);
  M2(v2, d2);
  M3(v3, d3);
}

//====================== Vectoring via RC ===================
void base2(int vel_x, int vel_y, int rot)
{
  //  theta = theta * 0.0174533;              //convert from deg angle to radian
  //  vel_x = magnitude * cos(theta);
  //  vel_y = magnitude * sin(theta);



  vel_x = map(vel_x, 990 , 2000  , -100, 100);
  vel_y = map(vel_y, 980 , 2000 , -100, 100);
  rot = map(rot, 990 ,  2000 , -50, +50);

  if (rot > -10 && rot < 10)
  {
    rot = 0;
  }

  const float sqrt3o2 = 1.0 * sqrt(3) / 2;
  float v1 = - vel_x + rot;
  float v2 = 0.5 * vel_x - sqrt3o2 * vel_y + rot;
  float v3 = 0.5 * vel_x + sqrt3o2 * vel_y + rot;

  d1 = 0;
  d2 = 0;
  d3 = 0;
  d1 = v1 < 0 ? -1 : 1;
  d2 = v2 < 0 ? -1 : 1;
  d3 = v3 < 0 ? -1 : 1;

  v1 = map(abs(v1), 0, 100, 0, 550);
  v2 = map(abs(v2), 0, 100, 0, 550);
  v3 = map(abs(v3), 0, 100, 0, 550);

  M1(v1, d1);
  M2(v2, d2);
  M3(v3, d3);
}

//============== Motor Functions ================================
void M1( int cps1_des, int dir1)
{
  if (dir1 == 1)
  {
    digitalWrite(inAPin1, HIGH);
    digitalWrite(inBPin1, LOW);
  }
  else if (dir1 == -1)
  {
    digitalWrite(inAPin1, LOW);
    digitalWrite(inBPin1, HIGH);
  }
  else if (dir1 == 0)
  {
    digitalWrite(inAPin1, LOW);
    digitalWrite(inBPin1, LOW);
  }

  err_new1 = (cps1_des - cps1);                 // calc error in counts
  err_d21 = err_new1 - err_d11;
  err_new1 = (Kp * err_new1) + (0 * err_old1) + (0 * err_d21) ;

  output1 = adj * (1.4919 * (err_new1));      //converting counts to PWM

  if (output1 > 250)
    output1 = 250;
  else if (output1 < 10)
    output1 = 0;

  analogWrite(PWMPin1, output1);
  err_old1 = err_new1;
  err_d11 = err_old1;
}

void M2( int cps2_des, int dir2)
{
  if (dir2 == 1)
  {
    digitalWrite(inAPin2, LOW);
    digitalWrite(inBPin2, HIGH);
  }
  else if (dir2 == -1)
  {
    digitalWrite(inAPin2, HIGH);
    digitalWrite(inBPin2, LOW);
  }
  else if (dir2 == 0)
  {
    digitalWrite(inAPin2, LOW);
    digitalWrite(inBPin2, LOW);
  }

  err_new2 = (cps2_des - cps2);               // calc error in counts
  err_d22 = err_new2 - err_d12;
  err_new2 = (Kp * err_new2) + (0 * err_old2) + (0 * err_d22);

  output2 = adj * (1.4919 * (err_new2));    //converting counts to PWM

  if (output2 > 250)
    output2 = 250;
  else if (output2 < 10)
    output2 = 0;

  analogWrite(PWMPin2, output2);
  err_old2 = err_new2;
  err_d12 = err_old2;
}

void M3( int cps3_des, int dir3)
{
  if (dir3 == 1)
  {
    digitalWrite(inAPin3, LOW);
    digitalWrite(inBPin3, HIGH);
  }
  else if (dir3 == -1)
  {
    digitalWrite(inAPin3, HIGH);
    digitalWrite(inBPin3, LOW);
  }
  else if (dir3 == 0)
  {
    digitalWrite(inAPin3, LOW);
    digitalWrite(inBPin3, LOW);
  }

  err_new3 = (cps3_des - cps3);            // calc error in counts
  err_d23 = err_new3 - err_d13;
  err_new3 = (Kp * err_new3) + (0 * err_old3) + (0 * err_d23) ;

  output3 = adj * (1.4919 * (err_new3)); //converting counts to PWM

  if (output3 > 250)
    output3 = 250;
  else if (output3 < 10)
    output3 = 0;

  analogWrite(PWMPin3, output3);
  err_old3 = err_new3;
  err_d13 = err_old3;
}


//=============== Timer ISR ======================================
ISR(TIMER1_COMPA_vect)                    // Speed calcullation
{
  if ((encoder3Pos != temp3) && (i == 0))
  {
    i++;
    temp1 = encoder1Pos;
    temp2 = encoder2Pos;
    temp3 = encoder3Pos;
  }
  if (i != 0)
  {
    cps1 = encoder1Pos - temp1;
    temp1 = encoder1Pos;
    cps2 = encoder2Pos - temp2;
    temp2 = encoder2Pos;
    cps3 = encoder3Pos - temp3;
    temp3 = encoder3Pos;
  }
}

//=============================== Encoder ISR ====================
void doEncoder1()
{
  encoder1Pos++;
}
void doEncoder2()
{
  encoder2Pos++;
}
void doEncoder3()
{
  encoder3Pos++;
}

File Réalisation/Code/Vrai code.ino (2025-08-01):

#include <FlexiTimer2.h>
#include <digitalWriteFast.h>

//SETUP DES CONSTANTES

//Globales
    int v = 255; //vitesse (en bit)

    volatile float pi = 3.141592653589793;


// Période d'échantillonnage en ms
    volatile long temps_initiale = millis(); //(en milliseconde)
    volatile long temps_precedent;
    volatile double T_echant = 10; // 1ms de période d'échantillionage 

//Encodeurs : N° de pin Arduino /  N° de pin d'interruption
    const int Encodeur1A = 2; const int interrupt_Enco1A = 0; 
    const int Encodeur1B = 3; const int interrupt_Enco1B = 1;

    const int Encodeur2A = 18; const int interrupt_Enco2A = 5;
    const int Encodeur2B = 19; const int interrupt_Enco2B = 4;

    const int Encodeur3A = 20; const int interrupt_Enco3A = 3;
    const int Encodeur3B = 21; const int interrupt_Enco3B = 2;



    volatile long ticks1 = 0; volatile long ticks1_offset = 0;
    volatile long ticks2 = 0; volatile long ticks2_offset = 0;
    volatile long ticks3 = 0; volatile long ticks3_offset = 0;
    

//Moteurs :
    const int Mot_1_Sens = 50 ;
    const int Mot_1_PWM = 8 ;

    const int Mot_2_Sens = 51 ;
    const int Mot_2_PWM = 10 ;

    const int Mot_3_Sens = 52 ;
    const int Mot_3_PWM = 12 ;


    volatile double omega1;
    volatile double omega2;
    volatile double omega3;


void setup() {

    Serial.begin(9200); 
    Serial.flush();



    //Encodeurs
        pinMode(Encodeur1A, INPUT); 
        pinMode(Encodeur1B, INPUT);

        pinMode(Encodeur2A, INPUT);
        pinMode(Encodeur2B, INPUT);

        pinMode(Encodeur3A, INPUT);
        pinMode(Encodeur3B, INPUT);


        // activation des résistances de pullup
        digitalWrite(Encodeur1A, HIGH);  
        digitalWrite(Encodeur1B, HIGH);  

        digitalWrite(Encodeur2A, HIGH);  
        digitalWrite(Encodeur2B, HIGH);
        
        digitalWrite(Encodeur3A, HIGH);  
        digitalWrite(Encodeur3B, HIGH);


        //Initialiation des interruptions
        attachInterrupt(interrupt_Enco1A, Codeur_Interupt_1A, CHANGE);
        attachInterrupt(interrupt_Enco1B, Codeur_Interupt_1B, CHANGE);

        attachInterrupt(interrupt_Enco2A, Codeur_Interupt_2A, CHANGE);
        attachInterrupt(interrupt_Enco2B, Codeur_Interupt_2B, CHANGE);

        attachInterrupt(interrupt_Enco3A, Codeur_Interupt_3A, CHANGE);
        attachInterrupt(interrupt_Enco3B, Codeur_Interupt_3B, CHANGE);

    //Moteurs
        pinMode(Mot_1_Sens,OUTPUT);
        pinMode(Mot_1_PWM, OUTPUT);

        pinMode(Mot_2_Sens,OUTPUT);
        pinMode(Mot_2_PWM, OUTPUT);

        pinMode(Mot_3_Sens,OUTPUT);
        pinMode(Mot_3_PWM, OUTPUT);



        digitalWrite(Mot_1_PWM, v );
        analogWrite(Mot_1_Sens, HIGH);

        digitalWrite(Mot_2_PWM, LOW );
        analogWrite(Mot_2_Sens, LOW);

        digitalWrite(Mot_3_PWM, v );  
        analogWrite(Mot_3_Sens, HIGH);


        FlexiTimer2::set(T_echant, T_echant/1000., Gestion_Moteurs); // résolution timer = 1 ms
        FlexiTimer2::start();


}


void loop() {

    if ( (millis() - temps_initiale) > 2500) {

        digitalWrite(Mot_1_PWM, 0 );  
        digitalWrite(Mot_1_Sens, LOW);

        digitalWrite(Mot_2_PWM, 0 );  
        digitalWrite(Mot_2_Sens, LOW);

        digitalWrite(Mot_3_PWM, 0 );  
        digitalWrite(Mot_3_Sens, LOW);
        
    }

}


void print_data() {
    
    Serial.println("------------------------------");
    Serial.print("Temps : "); Serial.println( (millis() - temps_initiale) ) ;
    Serial.println("------------------------------");
    Serial.println("         | Vitesse");
    Serial.println("------------------------------");
    Serial.print("Moteur 1 | "); Serial.print( omega1 ); Serial.println(" rad/seconde");
    Serial.println("------------------------------");
    Serial.print("Moteur 3 | "); Serial.print( omega3 ); Serial.println(" rad/seconde");
    Serial.println("------------------------------") ;
    Serial.println(" ");

}

void Gestion_Moteurs() {
    Moteur1();
    Moteur3();
}



void Moteur1() {
    

    ticks1_offset = ticks1;    
    Serial.println(ticks1_offset);
    ticks1 = 0;

    omega1 = ( (2*pi) / 544) * (ticks1_offset / T_echant ) *1000 ;



}

void Moteur3() {
    

    ticks3_offset = ticks3;    
    Serial.println(ticks3_offset);
    ticks3 = 0;

    omega3 = ( (2*pi) / 544) * (ticks3_offset / T_echant ) *1000 ;



}

//Fonctions de comptage des incrémentations des Encodeurs

    void Codeur_Interupt_1A() {
        Serial.print("Codeur_Interupt_1A");
        
        if (digitalReadFast(Encodeur1A) == digitalReadFast(Encodeur1B)) {
            ticks1--;
        }

        else {
            ticks1++;
        }
    }

    void Codeur_Interupt_1B() {
        Serial.println("Codeur_Interupt_1B");
        
        if (digitalReadFast(Encodeur1A) == digitalReadFast(Encodeur1B)) {
            ticks1++;
        }

        else {
            ticks1--;
        }
    }

    void Codeur_Interupt_2A() {
        Serial.println("Codeur_Interupt_2A");
        
        if (digitalReadFast(Encodeur2A) == digitalReadFast(Encodeur2B)) {
            ticks2--;
        }

        else {
            ticks2++;
        }
    }

    void Codeur_Interupt_2B() {
        Serial.println("Codeur_Interupt_2B");
        
        if (digitalReadFast(Encodeur2A) == digitalReadFast(Encodeur2B)) {
            ticks2++;
        }

        else {
            ticks2--;
        }
    }

    void Codeur_Interupt_3A() {

        Serial.println("Codeur_Interupt_3A");
        if (digitalReadFast(Encodeur3A) == digitalReadFast(Encodeur3B)) {
            ticks3--;
        }

        else {
            ticks3++;
        }
    }

    void Codeur_Interupt_3B() {
        Serial.println("Codeur_Interupt_3B");
        
        if (digitalReadFast(Encodeur3A) == digitalReadFast(Encodeur3B)) {
            ticks3++;
        }

        else {
            ticks3--;
        }
    }
    
